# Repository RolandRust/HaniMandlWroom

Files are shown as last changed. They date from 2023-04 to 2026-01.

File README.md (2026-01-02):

# HaniMandlWroom
HaniMandel für das Node MCU ESP32 38Pin Evaluation Board<br>

## Kompiliert nur mit Visual Studio Code. Mit der Arduino IDE gibts Probleme!

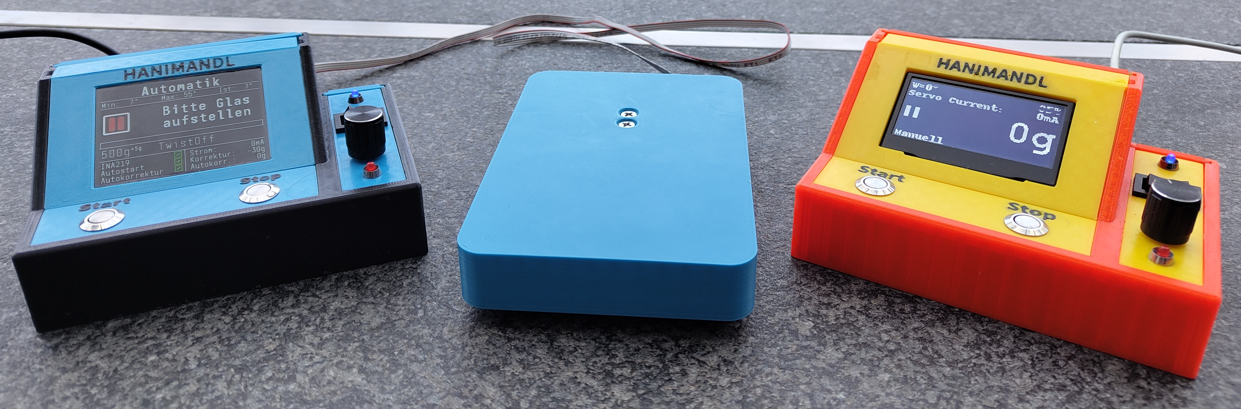
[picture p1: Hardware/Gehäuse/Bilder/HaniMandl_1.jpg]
HaniMandl_1


Dies ist eine abgeänderte Version von dem Orginal HaniMandl Projekt. Die Idee und Veröffentlichung wurde auf der Facebook-Gruppe ["Imkerei und Technik. Eigenbau"](https://www.facebook.com/groups/139671009967454) veröffentlicht.
Als Grundlage für dieses Projekt bediente ich mich am [develop Branch (V0.2.13)](https://github.com/ClemensGruber/hani-mandl/tree/develop) von Clemens Gruber.

## Projekt ligt momentan auf dem Eis

Open Source ist echt genial. Sich damit zu bereichern, ohne auch nur eine Änderung beizutragen, oder einfach nur die eigenen Daten für das Gehäuse zu veröffentlichen, ist einfach doof. Deshalb habe ich das Projekt erstmal auf Eis gelegt. Auch der Dev-Branch wird nicht mehr mit den neuesten Aktualisierungen versorgt. Ich gehe nun einen anderen Weg.

Aus dem kleinen wird der große – aber das wird weniger. Der Dreifach-Switch sowie Start- und Stop-Taster verschwinden. Übrig bleiben nur noch der Rotary-Encoder und ein 4-Zoll-TFT (und sollte ich mich irgendwo geirrt haben, hätte ich noch den Touch als Backup).

Wird es wieder Open Source? Wahrscheinlich nicht – wegen solchen doofen Vögel.

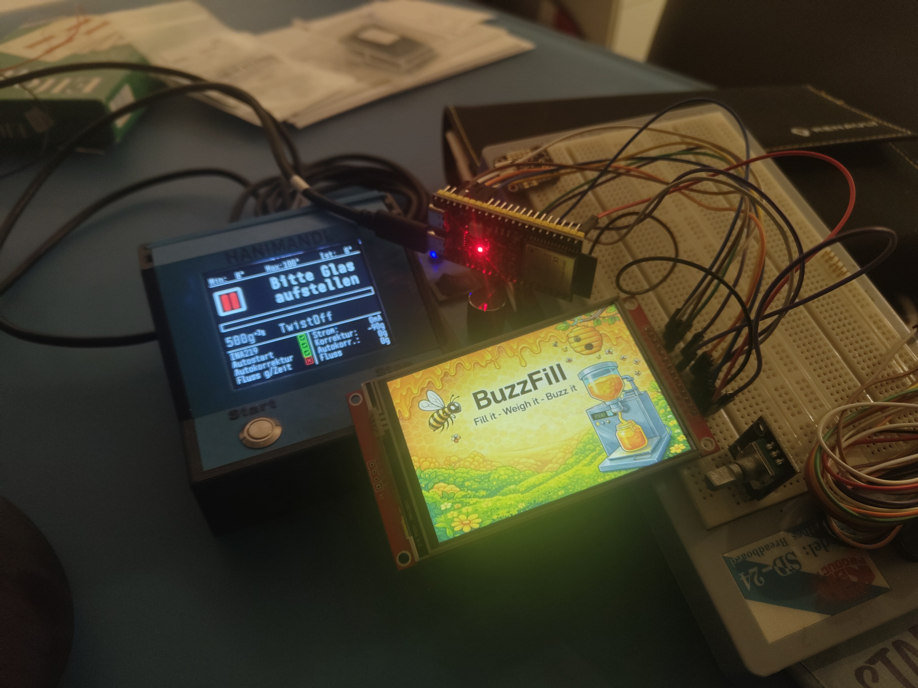
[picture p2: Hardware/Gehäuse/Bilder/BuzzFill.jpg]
BuzzFill


## Einstellungen
```
//
// Usereinstellung
//
// Könnt ihr auf eins lassen. User 2 und User 3 haben andere Glaseinstellungen
//
#define USER 1                    // 1 = Hanimandl Standart (ist die Default Einstellung so wie Ihr es gewohnt seit)
                                  // 2 = Gerold (Wird bei euch nicht funktionieren, da die Logos fehlen im ResPos)
                                  // 3 = Roli

//
// Hier den Code auf die verwendete Hardware einstellen
//
#define HARDWARE_LEVEL 1          // 1 = ESP32-WROOM 38Pin Connector
                                  // 2 = Heltec WiFi Kit V3 use on board display (nur in Verbindung mit DISPLAY_TYP 1)
                                  // 3 = Heltec WiFi Kit V3 use extern display   (nur in Verbindung mit DISPLAY_TYP 1)
#define SCALE_TYP 2               // 1 = 2kg Wägezelle
                                  // 2 = 5kg Wägezelle
#define SERVO_ERWEITERT           // definieren, falls die Hardware mit dem alten Programmcode mit Poti aufgebaut wurde oder der Servo zu wenig fährt
                                  // Sonst bleibt der Servo in Stop-Position einige Grad offen! Nach dem Update erst prüfen!
#define ROTARY_SCALE 1            // in welchen Schritten springt unser Rotary Encoder. 
                                  // Beispiele: KY-040 = 2, HW-040 = 1, für Poti-Betrieb auf 1 setzen
#define DISPLAY_TYPE 3            // 1 = 128x64 pixel OLED Display angeschlossen über I2C
                                  // 2 = 128x64 pixel OLED Display angeschlossen über SPI (nicht für das Heltec Module)
                                  // 3 = 320x240 pixel TFT Display ST7789 angeschlossen über SPI (nicht für das Heltec Module)
                                  // 99 = Oled über I2C und TFT über SPI für development
#define OTA 1                     // 0 = OTA Uptade ausgeschalten
                                  // 1 = OTA Update eingeschalten
#define DREHTELLER 0              // 0 = kein Drehteller
                                  // 1 = Drehteller vorhanden
#define CHANGE_MAC_ADDRESS_HM 1   // 0 = behalte die Orginale Mac Adresse
                                  // 1 = Wechsle die Mac Adresse auf {0x74, 0x00, 0x00, 0x00, 0x00, 0x01}
#define CHANGE_MAC_ADDRESS_TT 1   // 0 = Mac Adresse vom Drehteller ist die orginale
                                  // 1 = Mac Adresse vom Drehteller wurde gewechselt auf {0x74, 0x00, 0x00, 0x00, 0x00, 0x02}
//#define FEHLERKORREKTUR_WAAGE   // falls Gewichtssprünge auftreten, können diese hier abgefangen werden
                                  // Achtung, kann den Wägeprozess verlangsamen. Vorher Hardware prüfen.
//#define QUETSCHHAHN_LINKS       // Servo invertieren, falls der Quetschhahn von links geöffnet wird. Mindestens ein Exemplar bekannt

//
// Ende Benutzereinstellungen!
// 
```

## OTA Update
Neu kann man auch über WLAN eine neue Firmware aufspielen.
Diese Funktion wurde mit Hilfe von ElegantOTA implementiert: https://github.com/ayushsharma82/ElegantOTA
```
#define OTA 1                     // 0 = OTA Uptade ausgeschalten
                                  // 1 = OTA Update eingeschalten
```
Die SSID und das Passwort wird in dem File ./src/Resources/wifi.h eingetragen.
Um das OTA zu aktivieren betätigt die Start Taste wärend Ihr im Setupmenü Hauptbildschirm seid. Danach verbindet sich der HM mit dem WLAN und wenn es klappt wird die IP-Adresse angeteigt.
Diese könnt Ihr nun an eurem Computer eingeben (z.B. http://192.168.76.232/update) und danach ein Beliebiges Binary File über den Browser flaschen.  

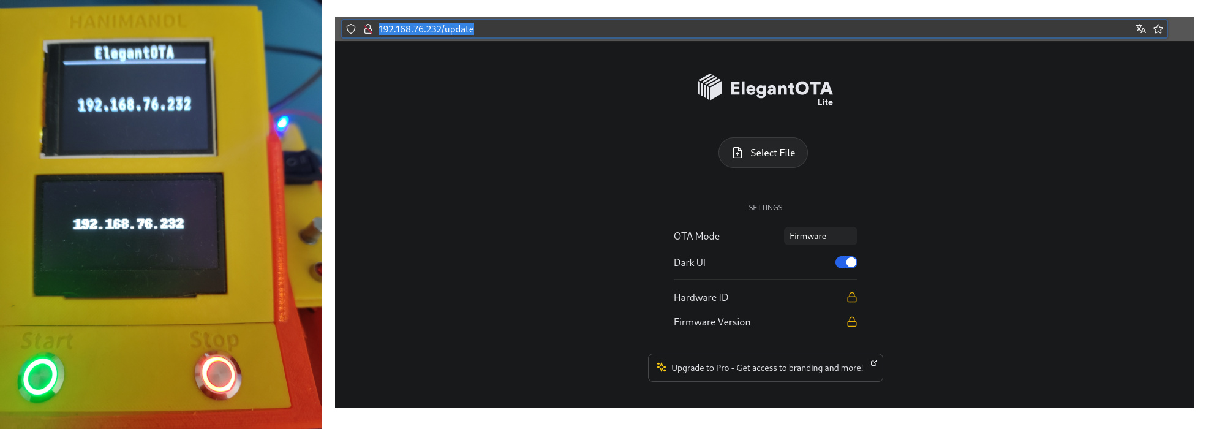
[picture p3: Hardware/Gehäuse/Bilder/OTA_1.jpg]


## Automatischer Volumenstrom beim Abfüllen
Unter Setup - Automatik kann neu ein Automatisch geregelter Volumenstrom eingestellt werden. Dies kan Hilfreich sein, wenn sehr flüssiger Honig abgefüllt wird.

## Bekannte Käferlein
Beim ersten Start ist der maximale Öffnungswinkel im Manuel und Automatik Betrieb auf 0. Dieser muss dann mit der Rotary eingestellt werden. Danach wird der Wert gespeichert. Ob das in der Alten Version auch schon so war, kann ich aus dem Kopf nicht sagen :-)

## Changelog
W.0.2
- OTA update implementiert
- Automatischer Volumenstrom beim Abfüllen implementiert (Nicht von mir getestet)
- Der HM kann nun auch über eine Sprachdatei die Menüsprache ändern (implementiert wurde bis jetzt Deutsch und Englisch)

W.0.3
- Die Sprache kann nun im Setup Menü ausgewählt werden (momentan Deutsch und Englisch. Ihr dürft gerne neue Sprachdateien machen und mir zukommen lassen)
- Funktion implementiert bei welcher man nach dem Tara das Glas wegnehmen kann und wider draufstellen mit eider Honigwabe oder sonstigem drin. (kann im Automatik Menü eingestellt werden)
- Hardware Level 2 und 3 hinzugefügt. Heltec Wifi Kit V3 (geht nur mit OLED Display)
- Drehteller Integriert

## Copyright

Die Software unterliegt dem gleichen Coryright und Anforderungen wie das Hauptprojekt.
Die Hardware (Gehäuse und PCB) sind von mir gemacht worden. Ich verzichte auf ein Copyriht für den Eigengebrauch. Auch wenn ich den Hanimandel nicht kommerziell vertreibe, gehören mir die Daten vom Gehäuse und PCB und diese dürfen nicht ohne meine Zustimmung kommerziell benützt werden.

## Benutzte Programme und Lizensen

Gehäuse: Ondsel/FreeCAD (keine Lizenz notwendig)<br>
PCB: DipTrace (kommerzielle Lizenz)

## Drehteller addon für den HaniMandel (HonigSchleppElesl)

zu finden unter: https://github.com/RolandRust/HonigSchleppElesl/

## Appell an dich

Bringt nix :-)

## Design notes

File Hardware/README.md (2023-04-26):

# HaniMandlWroom/Hardware
HaniMandel für das Node MCU ESP32 38Pin Evaluation Board
## Was findet man in diesem Ordner
In diesem Ordner findet man alles was mir der Hardware von HaniMandel zu tun hat

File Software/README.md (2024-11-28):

# HaniMandlWroom/Hardware
HaniMandel für das Node MCU ESP32 38Pin Evaluation Board
## Was findet man in diesem Ordner
In diesem Ordner findet man alles was mir der Software vom HaniMandel zu tun hat
## Einstellungen
```
//
// Usereinstellung
//
// Könnt ihr auf eins lassen. User 2 und User 3 haben andere Glaseinstellungen
//
#define USER 3                    // 1 = Hanimandl Standart (ist die default einstellung so wie Ihr es gewohnt seit)
                                  // 2 = Gerold (Wird bei euch nicht funktionieren, da die Logos fehlen im ResPos)
                                  // 3 = Roli

//
// Hier den Code auf die verwendete Hardware einstellen
//
#define HARDWARE_LEVEL 1          // 1 = ESP32-WROOM 38Pin Connector
#define SCALE_TYP 2               // 1 = 2kg Wägezelle
                                  // 2 = 5kg Wägezelle
#define SERVO_ERWEITERT           // definieren, falls die Hardware mit dem alten Programmcode mit Poti aufgebaut wurde oder der Servo zu wenig fährt
                                  // Sonst bleibt der Servo in Stop-Position einige Grad offen! Nach dem Update erst prüfen!
#define ROTARY_SCALE 1            // in welchen Schritten springt unser Rotary Encoder. 
                                  // Beispiele: KY-040 = 2, HW-040 = 1, für Poti-Betrieb auf 1 setzen
#define DISPLAY_TYPE 2            // 1 = 128x64 pixel OLED Display angeschlossen über I2C
                                  // 2 = 128x64 pixel OLED Display angeschlossen über SPI
                                  // 3 = 320x240 pixel TFT Display ST7789 angeschlossen über SPI
                                  // 99 = Oled über I2C und TFT über SPI für development
#define OTA 1                     // 0 = OTA Uptade ausgeschalten
                                  // 1 = OTA Update eingeschalten
#define DREHTELLER 1              // 0 = kein Drehteller
                                  // 1 = Drehteller vorhanden
#define CHANGE_MAC_ADDRESS_HM 1   // 0 = behalte die Orginale Mac Adresse
                                  // 1 = Wechsle die Mac Adresse auf {0x74, 0x00, 0x00, 0x00, 0x00, 0x01}
#define CHANGE_MAC_ADDRESS_TT 1   // 0 = Mac Adresse vom Drehteller ist die orginale
                                  // 1 = Mac Adresse vom Drehteller wurde gewechselt auf {0x74, 0x00, 0x00, 0x00, 0x00, 0x02}
//#define FEHLERKORREKTUR_WAAGE   // falls Gewichtssprünge auftreten, können diese hier abgefangen werden
                                  // Achtung, kann den Wägeprozess verlangsamen. Vorher Hardware prüfen.
//#define QUETSCHHAHN_LINKS       // Servo invertieren, falls der Quetschhahn von links geöffnet wird. Mindestens ein Exemplar bekannt

//
// Ende Benutzereinstellungen!
// 
```

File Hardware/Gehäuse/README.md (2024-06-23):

# HaniMandlWroom/Hardware/Gehäuse
HaniMandel für das Node MCU ESP32 38Pin Evaluation Board
## Was findet man in diesem Ordner
In diesem Ordner findet man alles was man braucht, um das Gehäuse und die Waage mir einem 3D-Drucker zu erstellen.

# 3D Bilder
## Gehäuse HaniMandl
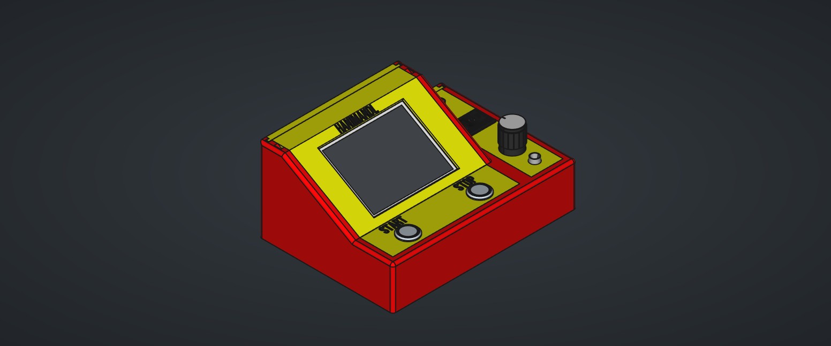
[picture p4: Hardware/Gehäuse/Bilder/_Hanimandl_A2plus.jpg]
Gehäuse HaniMandl

## Gehäuse Waage
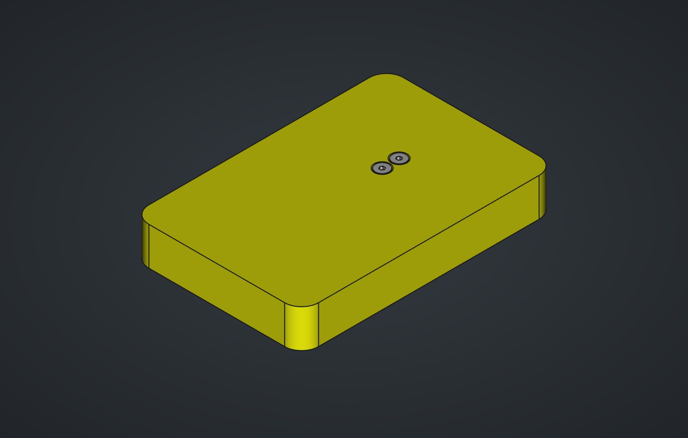
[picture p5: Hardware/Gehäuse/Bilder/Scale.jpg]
Gehäuse Waage


# Einzelteile Gehäuse Hanimandl
## Body (Filename: Bottom)
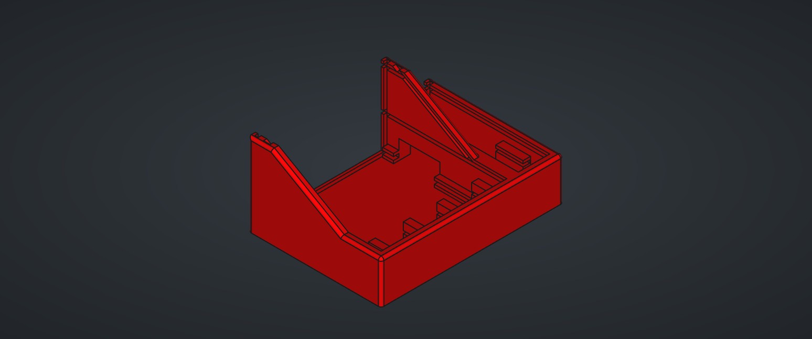
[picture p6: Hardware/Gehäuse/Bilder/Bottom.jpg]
Body

## Start/Stop Taster (Filename: Button)
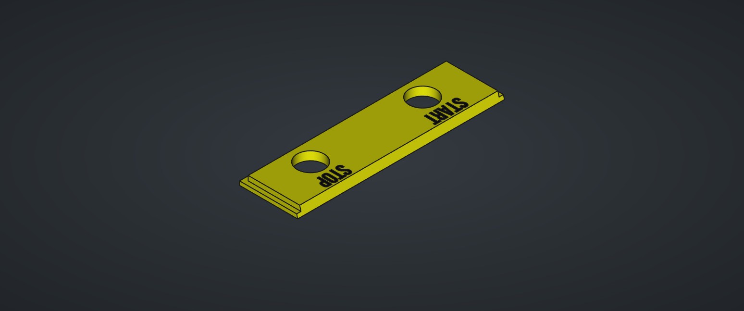
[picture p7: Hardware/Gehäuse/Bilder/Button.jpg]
Start/Stop Taster

## Display (Filename: Display_OLED)
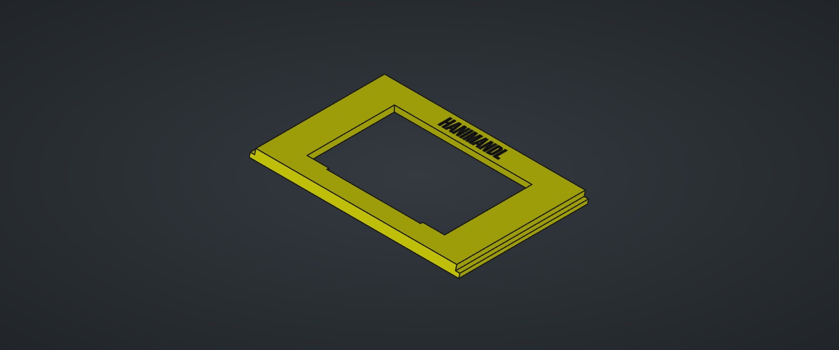
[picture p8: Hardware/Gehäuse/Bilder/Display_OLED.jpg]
Display

## Display 2.8TFT (Filename: Display_TFT)
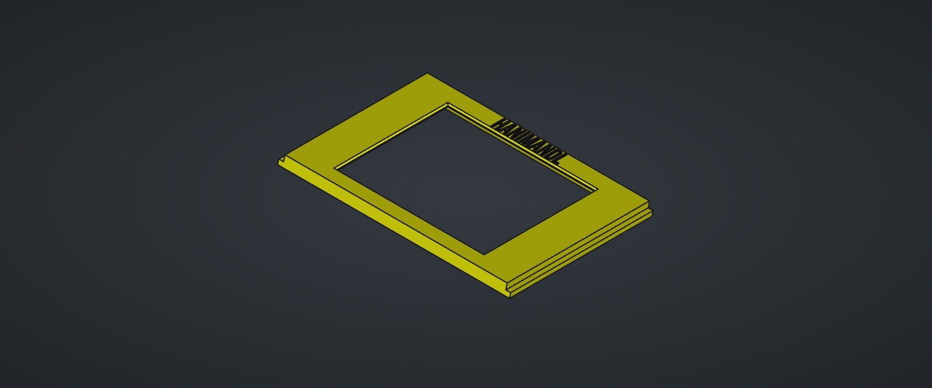
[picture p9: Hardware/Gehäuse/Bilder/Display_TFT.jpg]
Display

## Deckel top klein (Filename: Top)
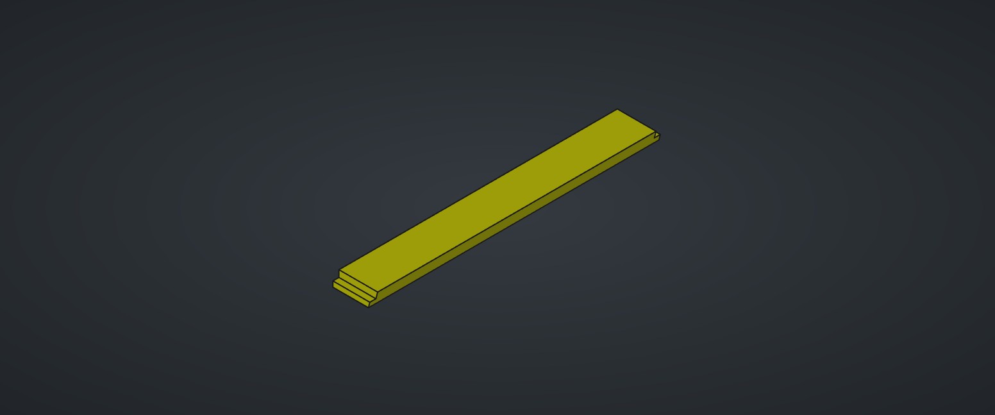
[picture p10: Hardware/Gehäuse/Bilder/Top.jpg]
Deckel top klein

## Deckel Bedienelemente (Filename: Rotary)
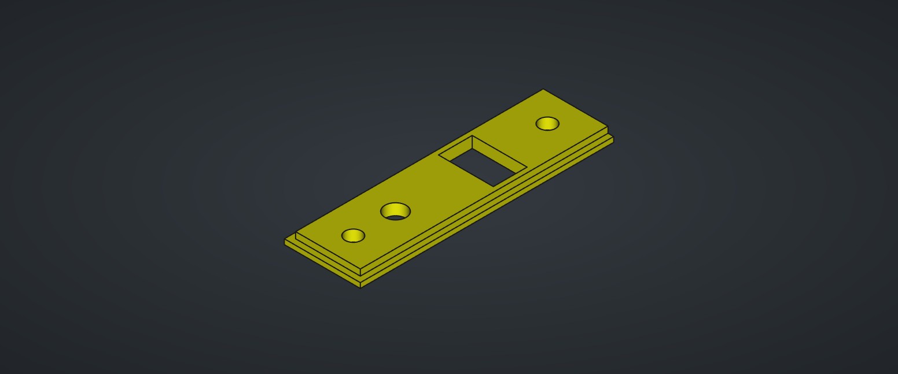
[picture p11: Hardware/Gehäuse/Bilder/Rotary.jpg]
eckel Bedienelemente

## Deckel Rückseite Bedienelemente (Filename: Back_Small)
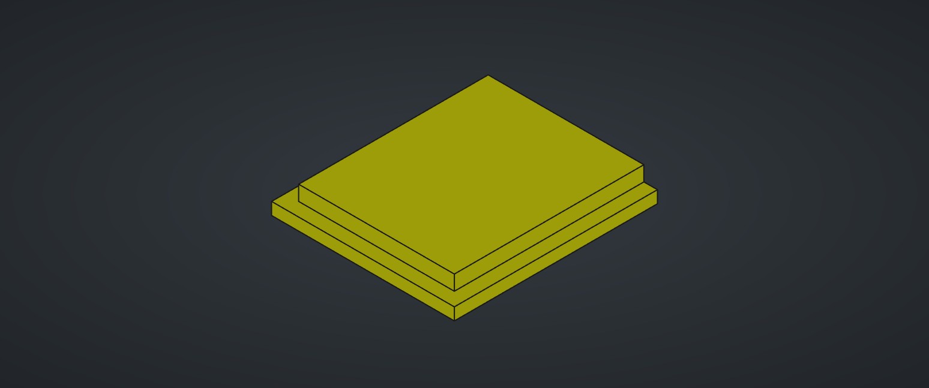
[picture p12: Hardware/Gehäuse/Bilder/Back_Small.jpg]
Deckel Rückseite Bedienelemente

## Deckel Rückseite Display oben (Filename: Back_Big_2)
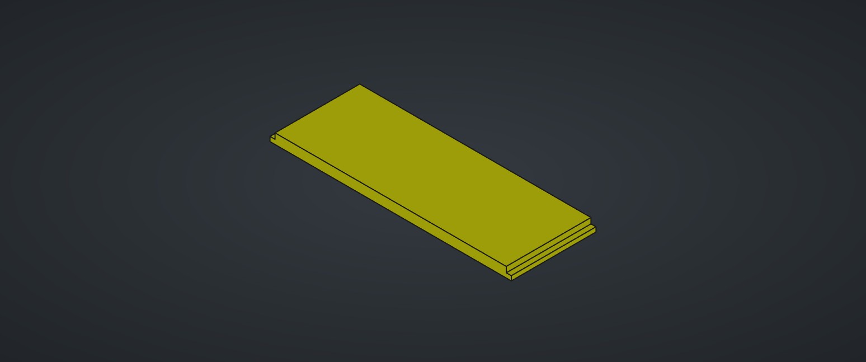
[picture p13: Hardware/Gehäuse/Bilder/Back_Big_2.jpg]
Deckel Rückseite Display oben

## Deckel Rückseite Display unten ohne USB (Filename: Back_Big_1)
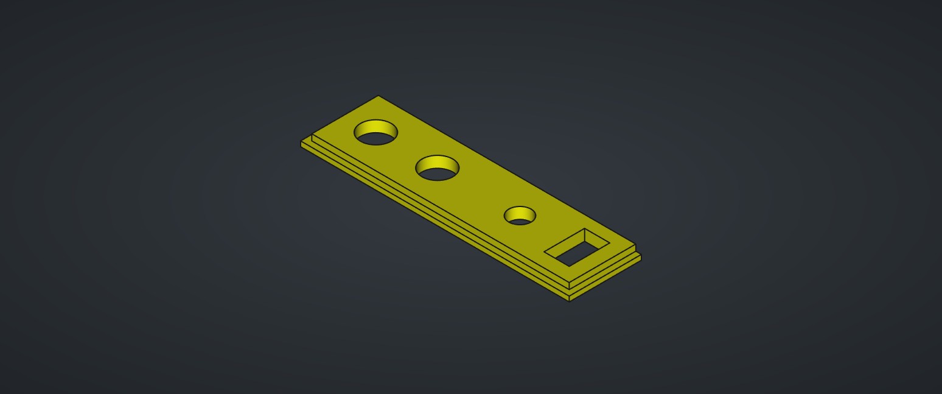
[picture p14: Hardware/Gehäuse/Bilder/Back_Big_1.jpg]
Deckel Rückseite Display unten ohne US

## Deckel Rückseite Display unten mit USB (Filename: Back_Big_1_USB)
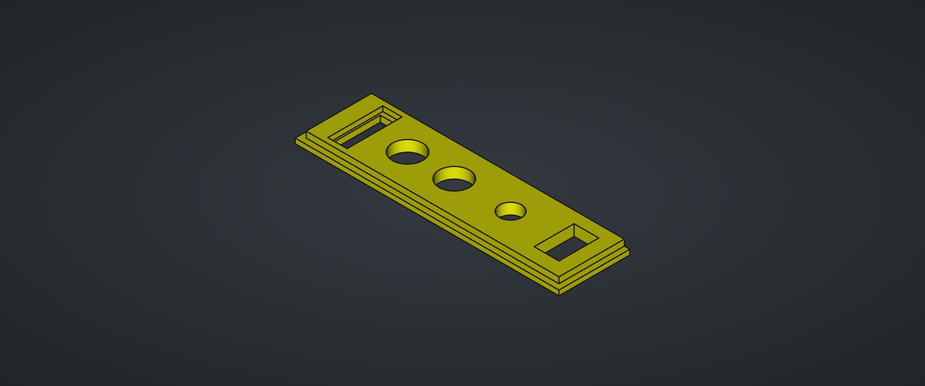
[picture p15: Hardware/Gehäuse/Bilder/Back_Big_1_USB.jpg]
Deckel Rückseite Display unten mit US


# Einzelteile Gehäuse Waage
## Waage oben (Filename: Scale_Top)
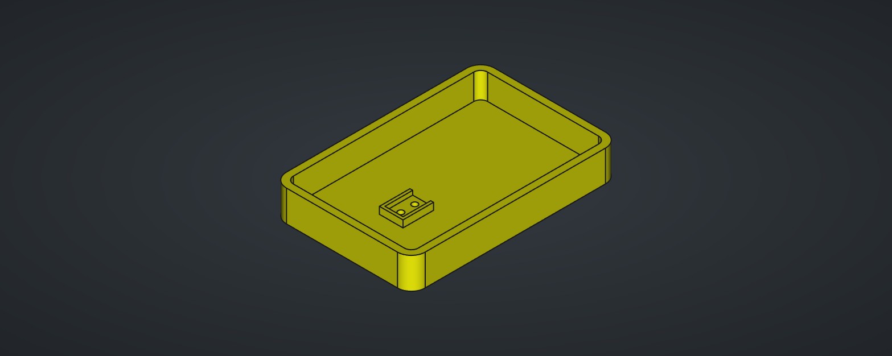
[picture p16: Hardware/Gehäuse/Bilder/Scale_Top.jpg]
Waage oben

## Waage unten (Filename: Scale_Bottom)
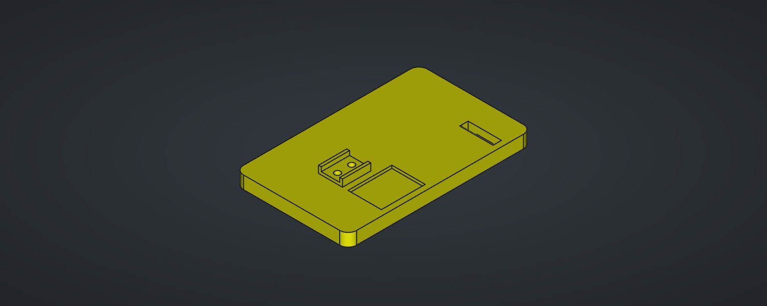
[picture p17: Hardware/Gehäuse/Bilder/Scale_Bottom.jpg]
Waage unten


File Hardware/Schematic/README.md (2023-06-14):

# HaniMandlWroom/Hardware/Schematic
HaniMandel für das Node MCU ESP32 38Pin Evaluation Board
## Was findet man in diesem Ordner
In diesem Ordner findet man alle Schaltpläne für den Hanimandl
## Schematic_Alle_Optionen.pdf
Vollbestückung mit allen Bestückungsoptionen
## Schematic_I2C-Display_No-INA219
Bestückungsoption mit einem I2C OLED 128x64 Pixel (SSD1306/SSD1309) und ohne INA219
## Schematic_I2C-Display_With-INA219
Bestückungsoption mit einem I2C OLED 128x64 (SSD1306/SSD1309) Pixel und mit INA219
## Schematic_SPI-Display_No-INA219
Bestückungsoption mit einem SPI OLED 128x64 Pixel (SSD1306/SSD1309) und ohne INA219<br>
TFT Display angesteuert über SPI mir 320x240 Pixel und dem ST7735 Displaytreiber und ohne INA219
## Schematic_SPI-Display_With-INA219
Bestückungsoption mit einem SPI OLED 128x64 (SSD1306/SSD1309) Pixel und mit INA219<br>
TFT Display angesteuert über SPI mir 320x240 Pixel und dem ST7735 Displaytreiber und mit INA219

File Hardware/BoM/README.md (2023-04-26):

# HaniMandlWroom/Hardware/BoM
HaniMandel für das Node MCU ESP32 38Pin Evaluation Board
## Was findet man in diesem Ordner
In diesem Ordner findet man die BoM für alle Bestückungswarianten von dem HaniMandl.

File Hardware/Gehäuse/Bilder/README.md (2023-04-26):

# HaniMandlWroom/Hardware/Gehäuse/Bilder
HaniMandel für das Node MCU ESP32 38Pin Evaluation Board
## Was findet man in diesem Ordner
In diesem Ordner findet man nur Bilder von dem Gehäuse des HaniMandels und der Waage

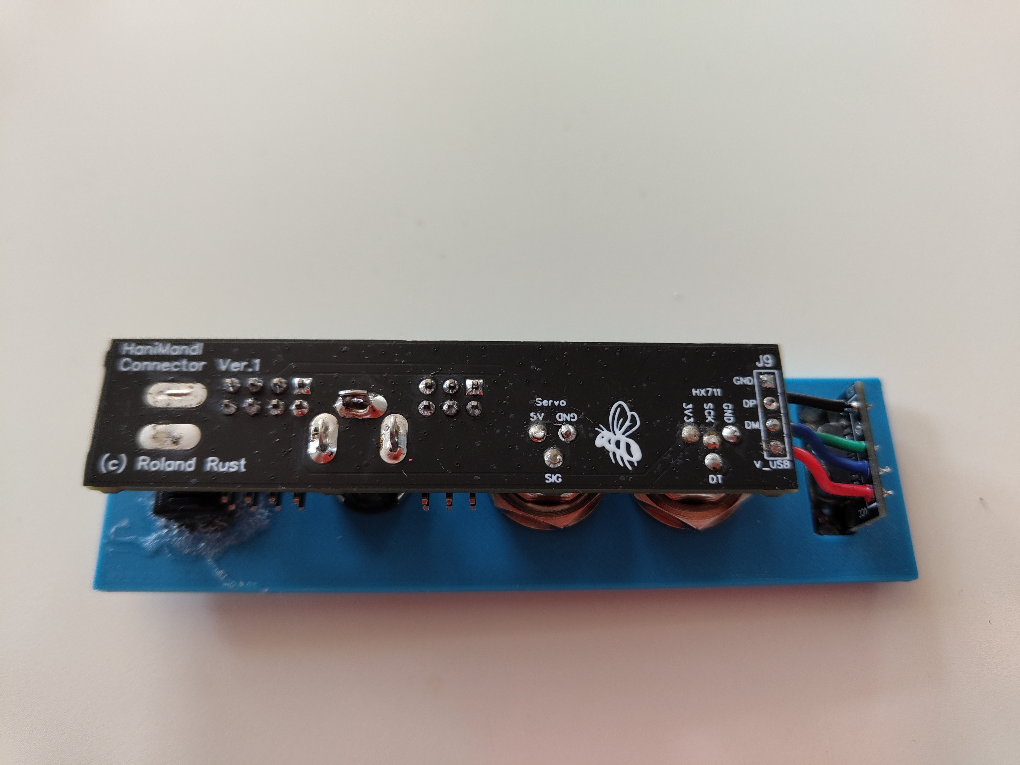
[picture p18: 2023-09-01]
Hardware/PCB/Pictures/363501928_1014343573054529_2882119520657273659_n.jpg

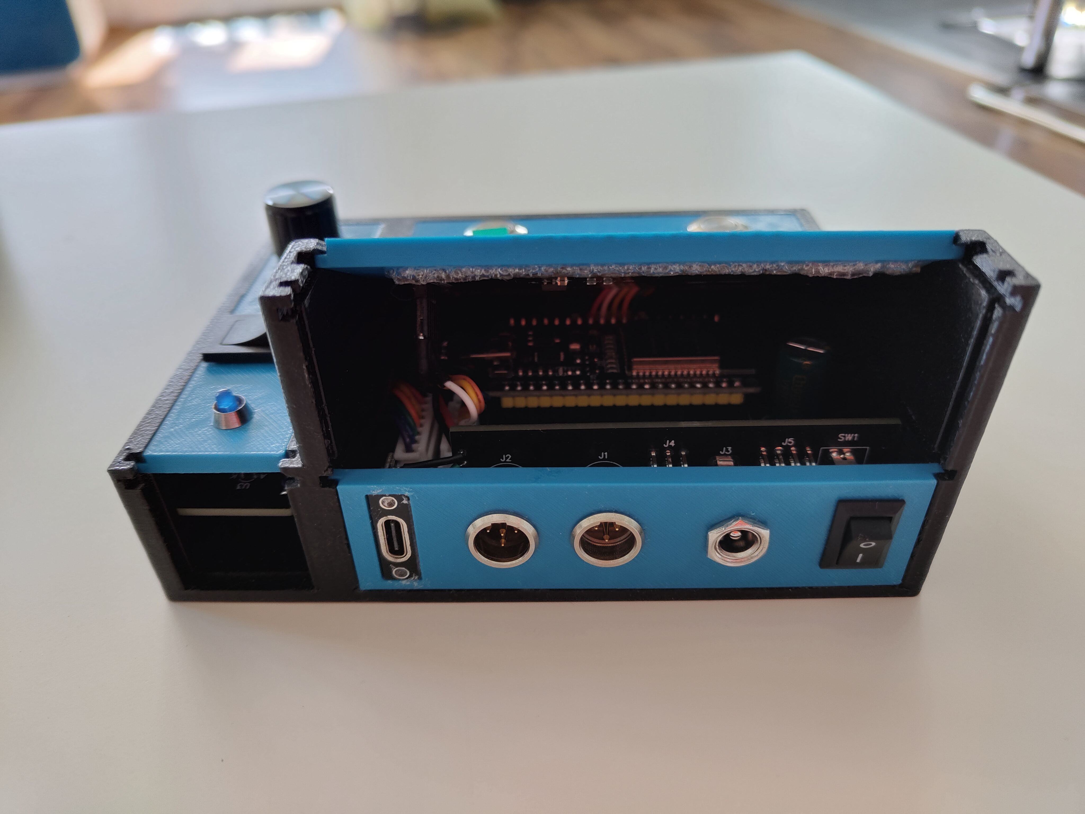
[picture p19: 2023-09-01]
Hardware/PCB/Pictures/363467502_966205168005585_3297736577394320761_n.jpg

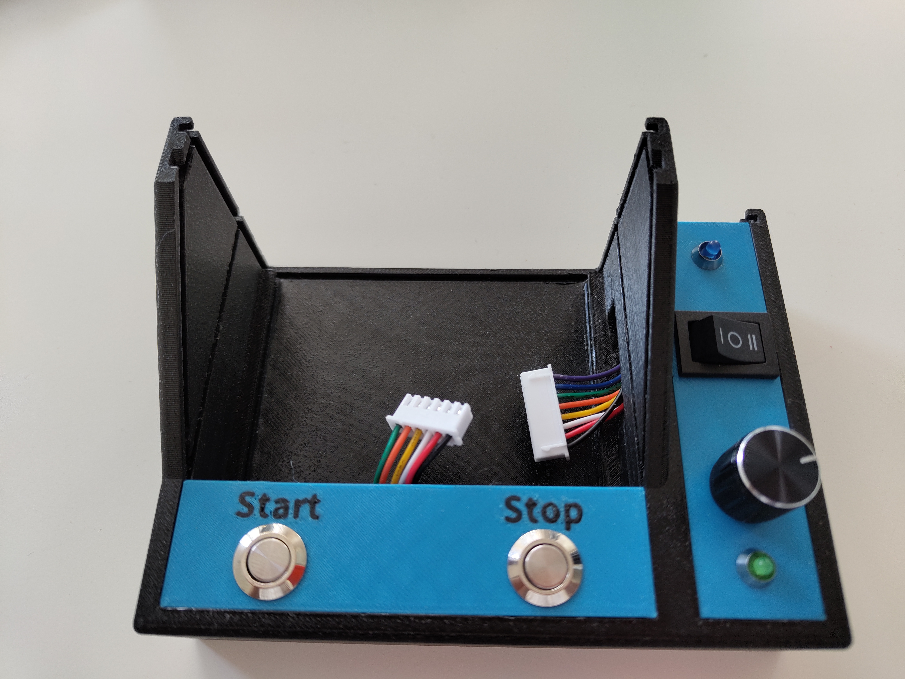
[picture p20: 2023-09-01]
Hardware/PCB/Pictures/363482455_1355187868746263_7550727053654712508_n.jpg

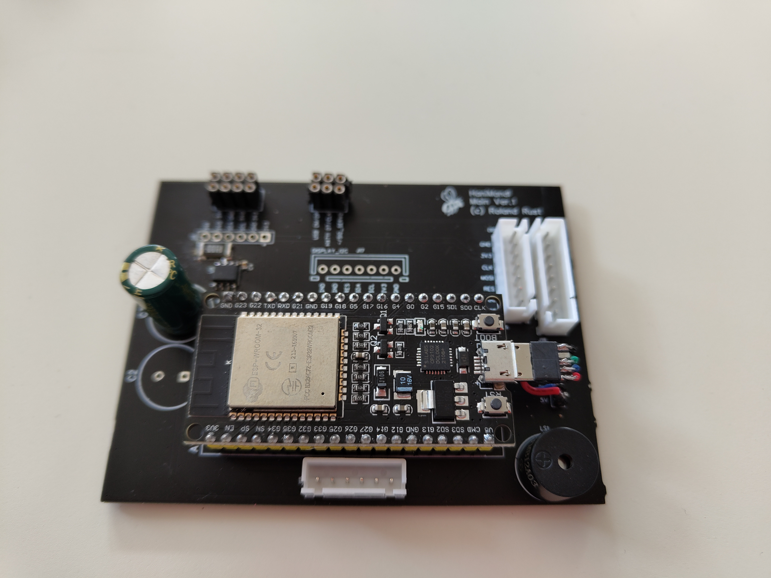
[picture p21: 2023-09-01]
Hardware/PCB/Pictures/363498172_692735799364409_5890090656269243421_n.jpg

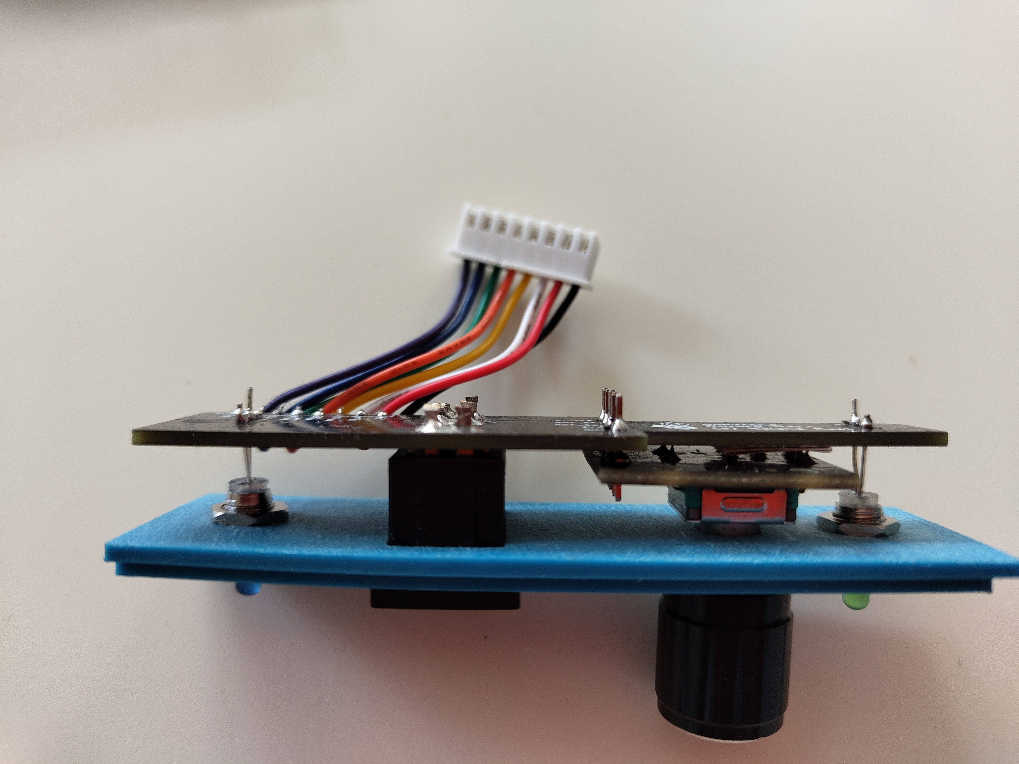
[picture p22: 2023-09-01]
Hardware/PCB/Pictures/363483665_819673566153577_7103739130340940338_n.jpg

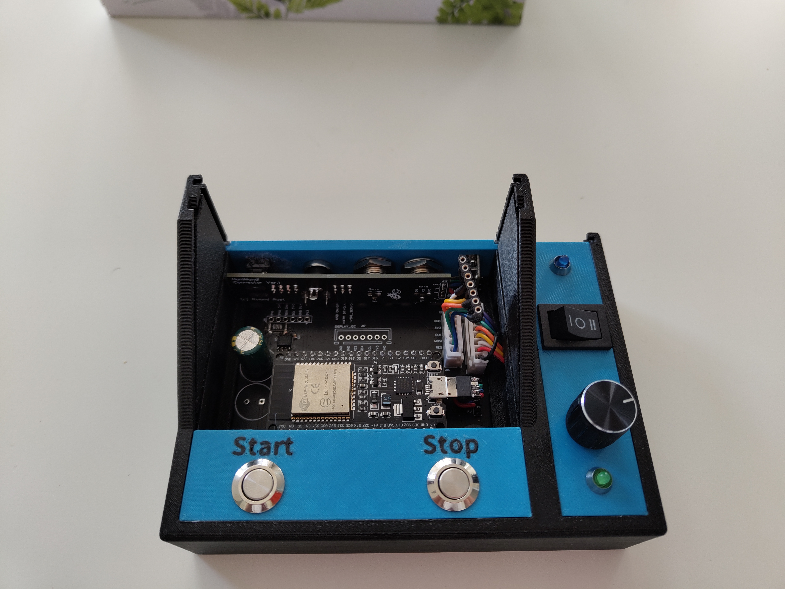
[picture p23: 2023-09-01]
Hardware/PCB/Pictures/363481905_1242739086406891_790757974748476911_n.jpg

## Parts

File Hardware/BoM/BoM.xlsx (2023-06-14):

 | Var1 | I2C OLED Display ohne INA219
 | Var2 | I2C OLED Display mit INA219
 | Var3 | SPI OLED Display ohne INA219
 | Var4 | SPI OLED Display mit INA219
 | Var5 | SPI TFT Display ohne INA219
 | Var6 | SPI TFT Display mit INA219
 | Hauptgehäuse
# | RefDes | Name | Quantity | Var1 | Var2 | Var3 | Var4 | Var5 | Var6 | Aliexpress Link (kann sein das er auf einmal nicht mehr funktioniert)
1 | - | Lochplatine 70x90mm | 1 | x | x | x | x | x | x | https://de.aliexpress.com/item/4000826804819.html
2 | A1 | Node MCU ESP32 38Pin Entwicklungsboard mit Wroom Modul | 1 | x | x | x | x | x | x | https://de.aliexpress.com/item/1005001636295529.html
3 | C1 | Elektrolyth Kondensator 2u2 | 1 | x | x | x | x | x | x
4 | LS1 | Buzzer (Tröte) | 1 | x | x | x | x | x | x | https://de.aliexpress.com/item/32885950305.html
5 | U1, U2 | Taster 2pol 12mm | 2 | x | x | x | x | x | x | https://de.aliexpress.com/item/4000310874353.html
6 | - | Leuchtdioden Halterung 3mm Metal | 2 | x | x | x | x | x | x | https://de.aliexpress.com/item/1005003385738351.html
7 | D1, D2 | Leuchtdioden 3mm | 2 | x | x | x | x | x | x | https://de.aliexpress.com/item/1005003432647675.html
8 | R1 | Widerstand 30K | 1 | x | x | x | x | x | x
9 | R2 | Widerstand 10K | 1 | x | x | x | x | x | x
10 | SW1 | Rotray Encoder mit Drehknopf (KY-040 oder HW-040) | 1 | x | x | x | x | x | x | https://de.aliexpress.com/item/1005001506432012.html
11 | U6 | SPDT On/Off/On Schalter 21x15mm | 1 | x | x | x | x | x | x | https://de.aliexpress.com/item/32986572167.html
12 | U3 | SPST Schalter 15x10mm | 1 | x | x | x | x | x | x | https://de.aliexpress.com/item/32987717201.html
13 | J1 | Power Buchse 2.1x5.5mm | 1 | x | x | x | x | x | x | https://de.aliexpress.com/item/32790883652.html
14 | U5 | Mini XLR Buchse 3Pin | 1 | x |  | x |  | x |  | https://de.aliexpress.com/item/1005004521851490.html?curPageLogUid=nE3oQnMNPnsI
15 | U7 | Mini XLR Buchse 3Pin | 1 |  | x |  | x |  | x
16 | U4 | Mini XLR Buchse 4Pin | 1 | x | x | x | x | x | x
17 | IC3 | INA219 Modul | 1 |  | x |  | x |  | x | https://de.aliexpress.com/item/1005004840860104.html
18 | IC1 | OLED Display 2.42 Zoll 126x64 | 1 | x | x |  |  |  |  | https://de.aliexpress.com/item/1005002766729064.html
19 | IC2 | OLED Display 2.42 Zoll 126x64 | 1 |  |  | x | x
20 | IC? | TFT Display 2.8 Zoll 320x240 | 1 |  |  |  |  | x | x | https://de.aliexpress.com/item/4000832671813.html
21 | - | Kabel mit Stecker um die Komponenten auf die Platine zu bringen |  | x | x | x | x | x | x | https://de.aliexpress.com/item/33011451583.html
 |  | Oprional wenn der USB Anschluss von dem Module nach ausen geführt wird
22 | - | USB C Buchse | 1 | x | x | x | x | x | x | https://de.aliexpress.com/item/1005003446036071.html
23 | - | Micro USB Stecker | 1 | x | x | x | x | x | x | https://de.aliexpress.com/item/32646590601.html
 | Waage
24 | - | Wäägezelle 5Kg | 1 | x | x | x | x | x | x | https://de.aliexpress.com/item/1005002483530537.html
25 | - | HX711 Module | 1 | x | x | x | x | x | x | https://de.aliexpress.com/item/33041823995.html?curPageLogUid=XPLqdXU4JuIP
 | Abfülleimer
26 |  | Servo 20Kg | 1 | x | x | x | x | x | x | https://de.aliexpress.com/item/32880295279.html
 | Abfülleimer
27 | - | Ein gutes 5V Netzteil | 1 | x | x | x | x | x | x

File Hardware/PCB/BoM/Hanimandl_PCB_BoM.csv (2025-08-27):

# | Quantity | RefDes | Manufacturer | Order Number | Description
1 | 1 | A1 | Diverse | - | ESP32 NodeMCU Module WLAN WiFi Development Board (use PinHeader to connect the Module))
2 | 2 | C1, C5 | Murata | GRM188R71E104K | Chip Monolithic Ceramic Capacitor X7R
3 | 2 | C2, C3 | Chemi-Con | EKMQ160ETD222MJ20S | Miniature Aluminium Electrolytic Capacitor 2200uF 16V ±20% 10x20mm
4 | 1 | D1 | Nexperia | NSR0130P2T5G | 30V Schottky Barrier Diode, 30V / 100mA, 2-Pin SOD-923
5 | 1 | J1 | Spectra | 7102-M3M | Mini XLR Connector 3pol. male
6 | 1 | J2 | Spectra | 7102-M4M | Mini XLR Connector 4pol. male
7 | 1 | J3 | Lumberg | 1614 19 | 2.1mm Power Plug
8 | 1 | J4 | Harwin | M20-9740346 | Pin Header 100min 2x3 right angle
9 | 1 | J5 | Harwin | M20-9740446 | Pin Header 100min 2x4 right angle
10 | 2 | J6, J7 | Bomin Electronic | EJ12-211PM | Ultra Short Metal Button
11 | 3 | J8, J10, J11 | Samtec | TSW-104-07-G-S | 1x4 Pol Connector 100mil
12 | 2 | J9, J19 | Samtec | TSW-104-07-G-S | 1x4 Pol Connector 100mil
13 | 1 | J12 | Samtec | TSW-104-07-G-S | 1x4 Pol Connector 100mil
14 | 1 | J13 | Preci-dip | 803-87-006-65-001101 | Socket 2x3, 2.54mm, height 7mm
15 | 1 | J14 | Preci-dip | 803-87-008-65-001101 | Socket 2x4, 2.54mm, height 7mm
16 | 1 | J15 | Diverse | - | JST XH 6pol Connector 2.54mm (not orginal JST standart)
17 | 2 | J16, J17 | Diverse | - | JST XH 7pol Connector 2.54mm (not orginal JST standart)
18 | 1 | J18 | Diverse | - | JST XH 8pol Connector 2.54mm (not orginal JST standart)
19 | 1 | LS1 | Soberton Inc. | WST-1203UX | AUDIO INDICATOR 82 DB 3 VDC 2300 HZ
20 | 1 | R1 | YAGEO | RC0603JR-0715KL | SMD-Resistor 15kOhm 5 % 100mW 0603
21 | 2 | R2, R7 | YAGEO | PE2512FKE7W0R1L | Resistor 0R1 1% 2W 2512
22 | 4 | R3, R4, R8, R9 | YAGEO | RC0603JR-0710KL | SMD-Resistor 10kOhm 5 % 100mW 0603
23 | 1 | R5 | YAGEO | RC0603JR-071KL | SMD-Resistor 1kOhm 5 % 100mW 0603
24 | 1 | R6 | YAGEO | RC0603JR-0730KL | SMD-Resistor 30kOhm 5 % 100mW 0603
25 | 1 | SW1 | Yueqing Hegxing Electrical | KCD1-11 | 2 pin ON - OFF small rocker switch
26 | 1 | SW2 | IDUINO | SE055 | Rotary Encoder development board, KY-040
27 | 2 | U1, U5 | Texas Instruments | INA219BIDR | INA219 Zero-Drift, Bidirectional Current/Power Monitor with I2C interface
28 | 1 | U2 | Yueqing Hegxing Electrical | KCD1-00-103 | Rocker Switch 6A@250VAC ON-OFF-ON SPST
29 | 1 | U3 | QUADRIOS | 2111O151 | LED blue, 3mm
30 | 1 | U4 | QUADRIOS | 2111O155 | LED red, 3mm

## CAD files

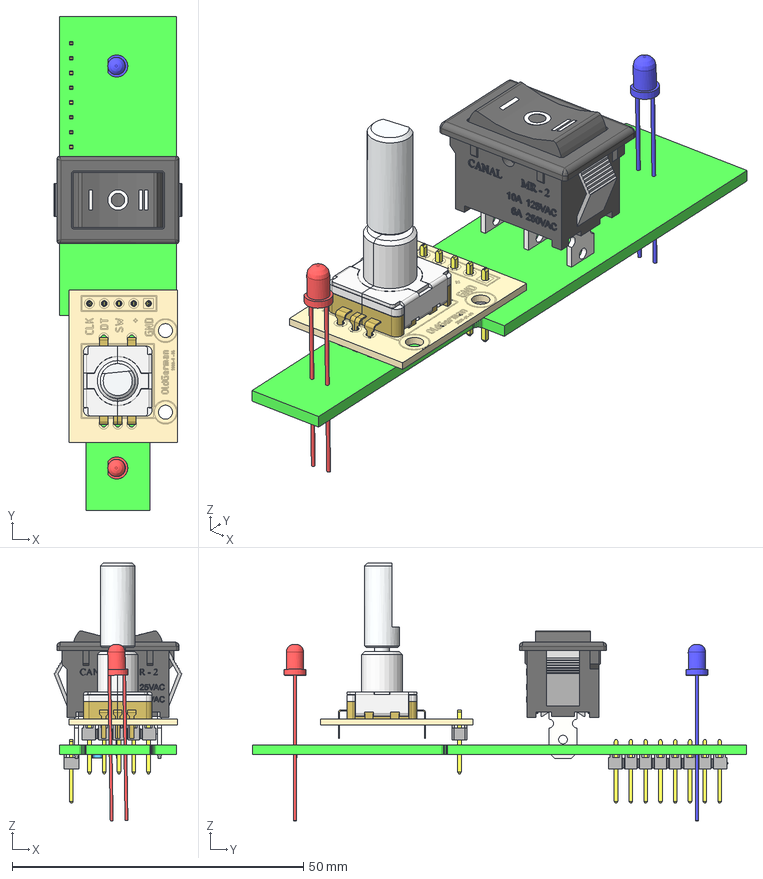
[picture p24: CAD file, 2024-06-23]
Hardware/Gehäuse/Ondsel(FreeCAD)/_STEP_PCB_Rotary.FCStd
21.9 x 84.8 x 44.3 mm
Board__Rotary
TSW-108-07-G-S
TSW-108-07-G-S006
RES_0603
RES_0607
KY-040_Rotary_Encoder_1
KY-040_Rotary_Encoder_019
KY-040_Rotary_Encoder_020
KY-040_Rotary_Encoder_021
KY-040_Rotary_Encoder_022
KY-040_Rotary_Encoder_023
KY-040_Rotary_Encoder_024
KY-040_Rotary_Encoder_025
Rocker_Switch_-_On-Off-On_05
Rocker_Switch_-_On-Off-On_041
Rocker_Switch_-_On-Off-On_042
Rocker_Switch_-_On-Off-On_043
Rocker_Switch_-_On-Off-On_044
Rocker_Switch_-_On-Off-On_045
Rocker_Switch_-_On-Off-On_046
Rocker_Switch_-_On-Off-On_047
Rocker_Switch_-_On-Off-On_048
Rocker_Switch_-_On-Off-On_049
Rocker_Switch_-_On-Off-On_050
Rocker_Switch_-_On-Off-On_051
Rocker_Switch_-_On-Off-On_052
Rocker_Switch_-_On-Off-On_053
Rocker_Switch_-_On-Off-On_054
Rocker_Switch_-_On-Off-On_055
Rocker_Switch_-_On-Off-On_056
LED_3mm_Head_blue
LED_3mm_Head_blue006
LED_3mm_Head_red
LED_3mm_Head_red006

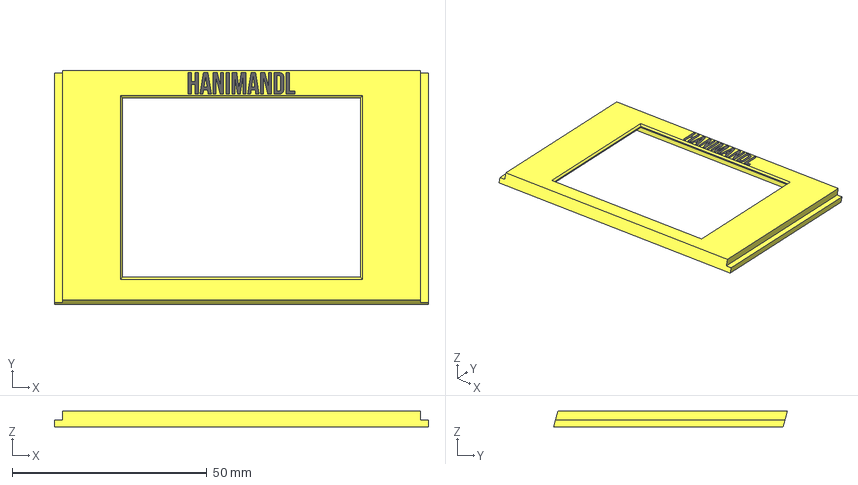
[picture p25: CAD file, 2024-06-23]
Hardware/Gehäuse/STEP/Display_TFT.step
96.0 x 60.0 x 4.00 mm

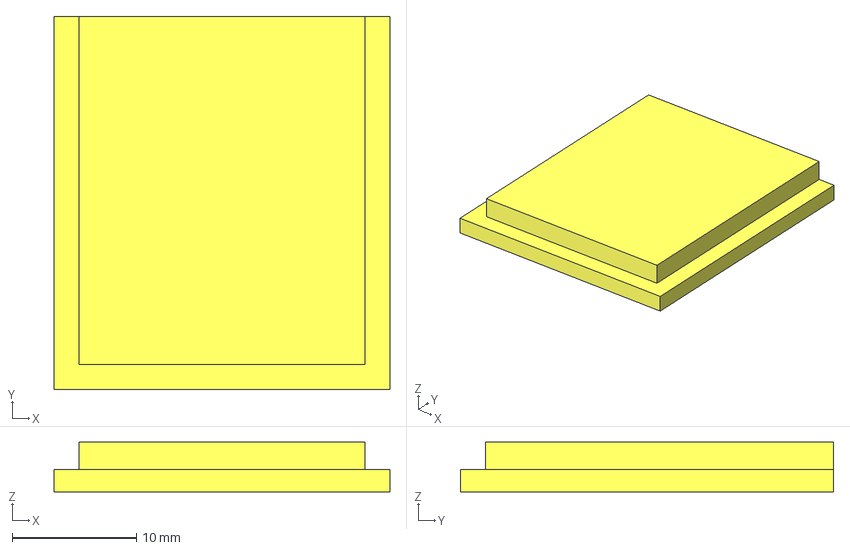
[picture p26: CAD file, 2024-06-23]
Hardware/Gehäuse/Ondsel(FreeCAD)/Back_Small.FCStd
27.0 x 30.0 x 4.00 mm

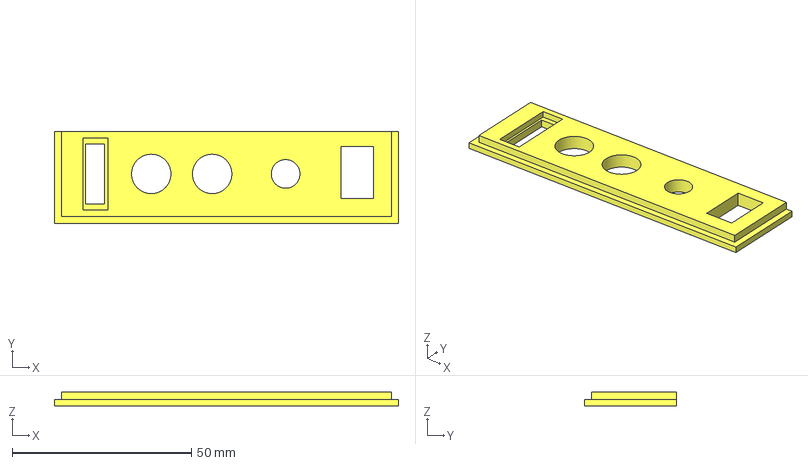
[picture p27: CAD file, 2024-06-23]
Hardware/Gehäuse/Ondsel(FreeCAD)/Back_Big_1_USB.FCStd
96.0 x 25.8 x 4.00 mm

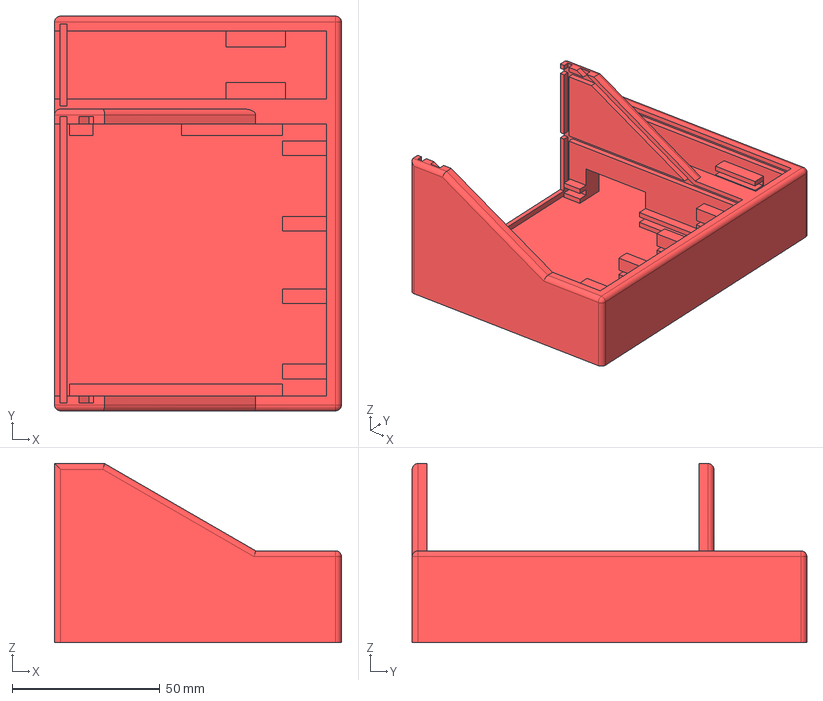
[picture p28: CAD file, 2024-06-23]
Hardware/Gehäuse/STEP/Bottom.step
97.0 x 133.4 x 60.5 mm

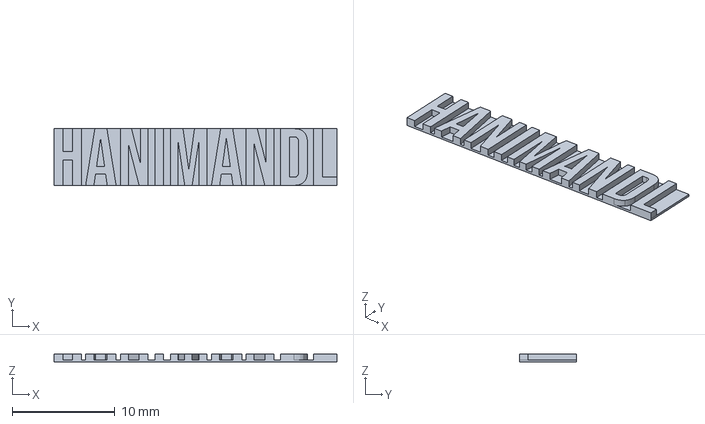
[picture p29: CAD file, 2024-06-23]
Hardware/Gehäuse/Ondsel(FreeCAD)/Hanimandl.FCStd
27.5 x 5.50 x 0.8 mm

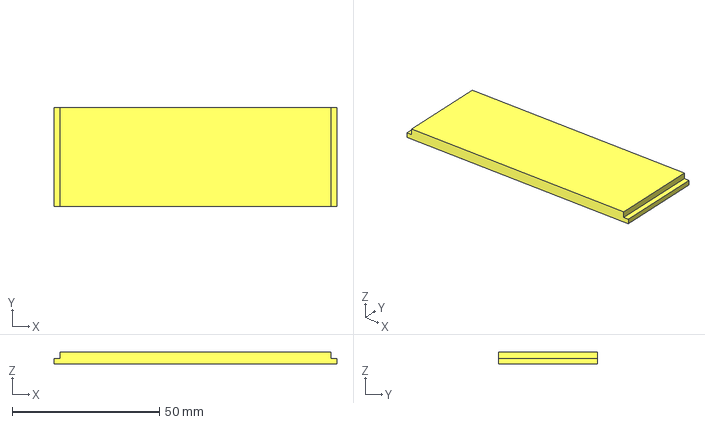
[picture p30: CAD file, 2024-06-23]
Hardware/Gehäuse/STEP/Back_Big_2.step
96.0 x 33.7 x 4.00 mm

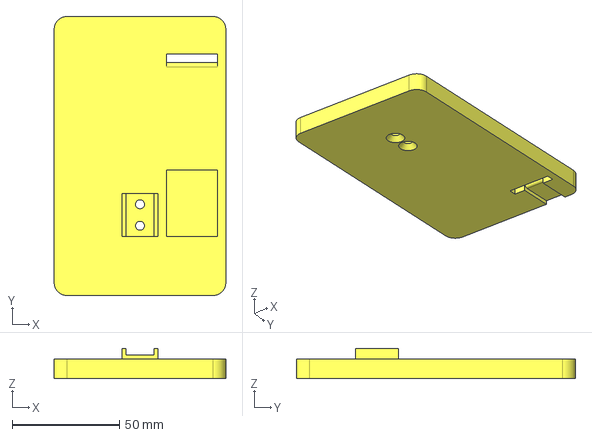
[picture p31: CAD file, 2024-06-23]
Hardware/Gehäuse/Ondsel(FreeCAD)/Scale_Bottom.FCStd
80.0 x 130.0 x 14.0 mm

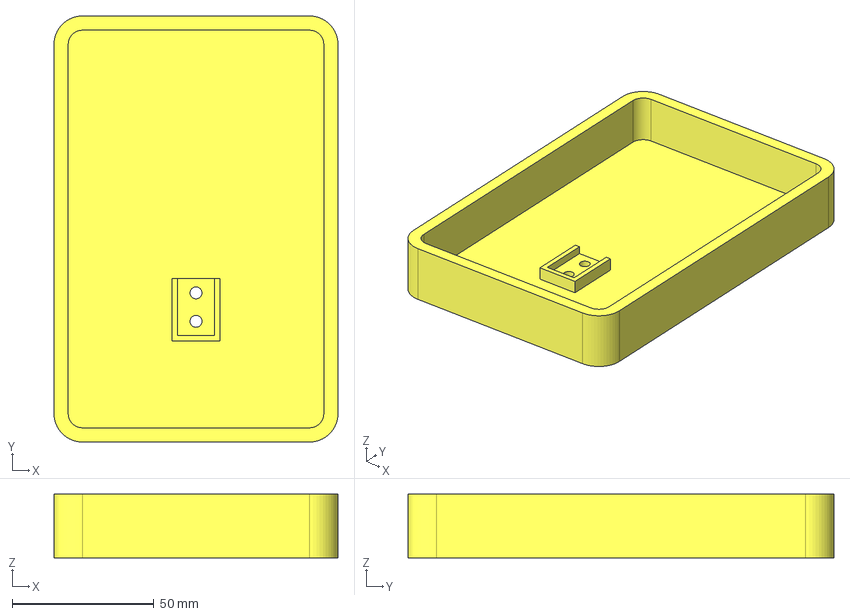
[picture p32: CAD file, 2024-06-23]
Hardware/Gehäuse/STEP/Scale_Top.step
100.0 x 150.0 x 22.4 mm

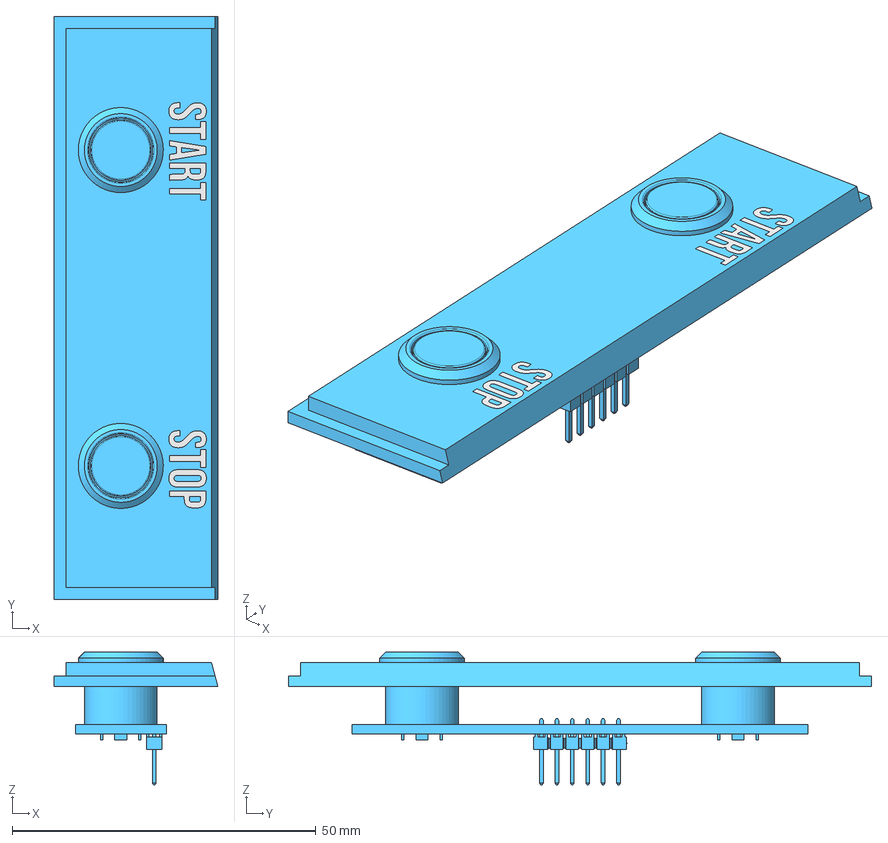
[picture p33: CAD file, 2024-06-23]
Hardware/Gehäuse/Ondsel(FreeCAD)/_Button.FCStd
27.0 x 96.0 x 21.9 mm
_STEP_PCB_Buttons_001
Buttons_001
Start_001
Stop_001

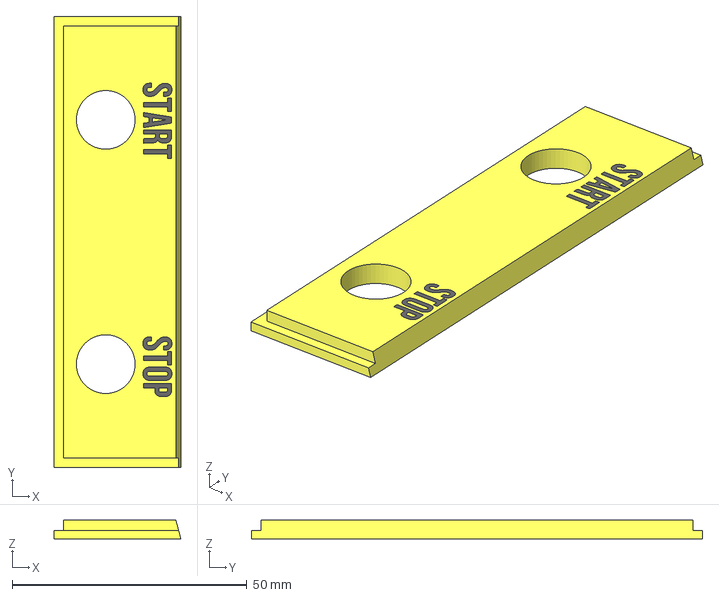
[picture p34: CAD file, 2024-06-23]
Hardware/Gehäuse/STEP/Button.step
27.0 x 96.0 x 4.00 mm

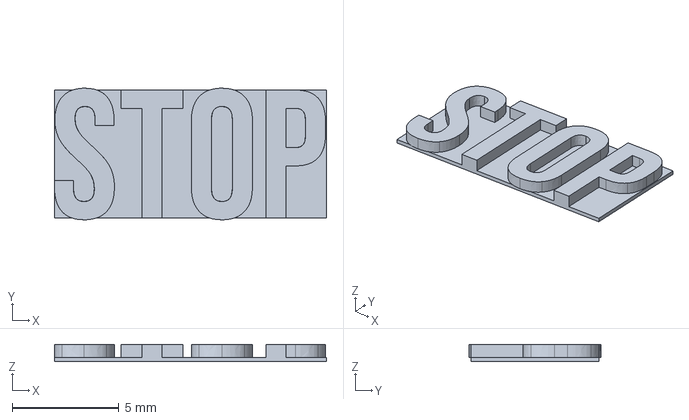
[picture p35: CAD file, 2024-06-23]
Hardware/Gehäuse/Ondsel(FreeCAD)/Stop.FCStd
12.8 x 6.17 x 0.8 mm

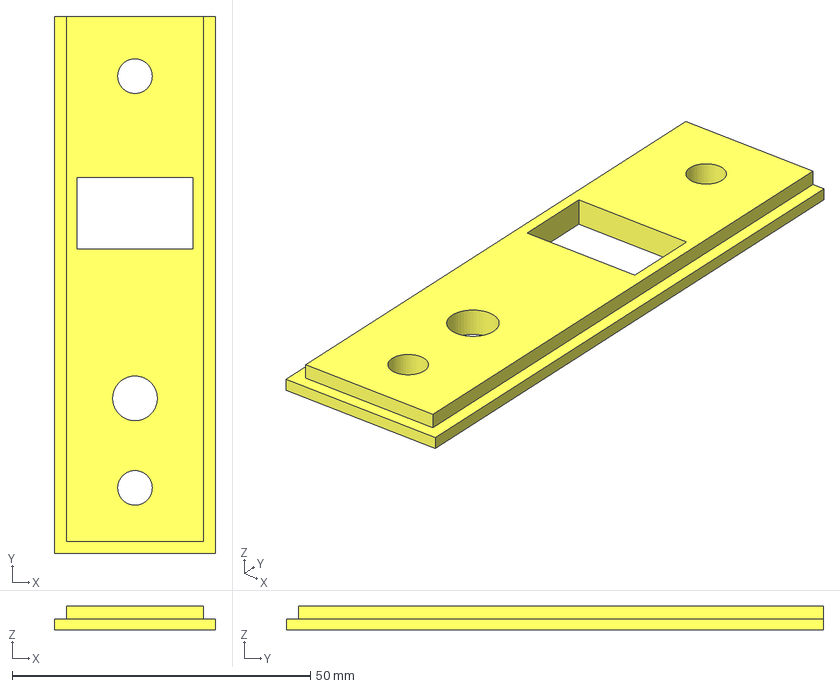
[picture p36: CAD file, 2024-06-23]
Hardware/Gehäuse/STEP/Rotary.step
27.0 x 90.0 x 4.00 mm

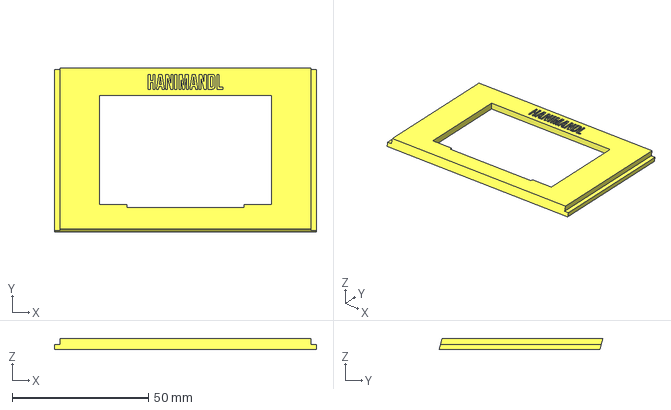
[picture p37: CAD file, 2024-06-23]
Hardware/Gehäuse/Ondsel(FreeCAD)/Display_OLED.FCStd
96.0 x 60.0 x 4.00 mm

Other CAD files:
Hardware/Gehäuse/STEP/Back_Small.step
Hardware/Gehäuse/STEP/Back_Big_1_USB.step
Hardware/Gehäuse/Ondsel(FreeCAD)/_STEP_PCB_Power.FCStd
Hardware/Gehäuse/STEP/Top.step
Hardware/Gehäuse/Ondsel(FreeCAD)/Back_Big_1.FCStd
Hardware/Gehäuse/Ondsel(FreeCAD)/Back_Big_2.FCStd
Hardware/Gehäuse/Ondsel(FreeCAD)/Bottom.FCStd
Hardware/Gehäuse/Ondsel(FreeCAD)/Buttons.FCStd
Hardware/Gehäuse/Ondsel(FreeCAD)/Display_TFT.FCStd
Hardware/Gehäuse/Ondsel(FreeCAD)/Rotary.FCStd
Hardware/Gehäuse/Ondsel(FreeCAD)/Scale_Top.FCStd
Hardware/Gehäuse/Ondsel(FreeCAD)/Start.FCStd
Hardware/Gehäuse/Ondsel(FreeCAD)/Top.FCStd
Hardware/Gehäuse/Ondsel(FreeCAD)/_Back_Big_1_USB.FCStd
Hardware/Gehäuse/Ondsel(FreeCAD)/_Display_OLED.FCStd
Hardware/Gehäuse/Ondsel(FreeCAD)/_Display_TFT.FCStd
Hardware/Gehäuse/Ondsel(FreeCAD)/_Rotary.FCStd
Hardware/Gehäuse/Ondsel(FreeCAD)/_STEP_PCB_Buttons.FCStd
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

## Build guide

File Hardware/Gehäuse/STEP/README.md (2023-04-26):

# HaniMandlWroom/Hardware/Gehäuse/STEP
HaniMandel für das Node MCU ESP32 38Pin Evaluation Board
## Was findet man in diesem Ordner
In diesem Ordner findet man alle STEP Files von dem HaniMandel Gehäuse und der Waage für den 3D-Druck

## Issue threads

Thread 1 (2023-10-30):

ROTARY_SCALE 2 small problem

Frank-Bemelman, 2023-10-30:
Hi there!

Tried your software. My rotary encoder gives 2 steps per click.
So I adjusted #define ROTARY_SCALE 2

When set to 1, it is difficult to navigate the setup menu, as it makes two steps per click of the rotary knob.
When set to 2, the navigation makes nice steps, but only the 4 first items are reachable.

So, around line #2970, I changed as shown below. Now, the full menu is accesible.

BTW, I also changed the direction of the knob, it seems to me that -1 for the step value gives an unnatural behaviour,
but I guess this might be personal. For me, a clockwise rotation should select in downwards fashion.

initRotaries(SW_MENU, lastpos, -1, MenuepunkteAnzahl, 1);
  while (modus == MODE_SETUP and (digitalRead(switch_setup_pin)) == HIGH) {
    if (rotaries[SW_MENU].Value < 0) {
      rotaries[SW_MENU].Value = (MenuepunkteAnzahl * ROTARY_SCALE) - 1;
    }
    else if (rotaries[SW_MENU].Value > ((MenuepunkteAnzahl * ROTARY_SCALE) - 1)) {
      rotaries[SW_MENU].Value = 0;
    }

Keep up the good work,
Cheers.
Frank

RolandRust, 2023-11-16:
Hello,
thx for the Input.
I tested the Rotary only with the KY-040. Maybe I should also order a HW-040 RSW.
I'll implement your changes and will test the Program.  You are right. The HW-040 makes 2 Input Signals per one step, so You will never reach the end of the Menu.
BR
Roli

RolandRust, 2024-02-04:
Should be now fixed in the Developer Branch. But not tested.

RolandRust, 2024-06-23:
Should be solved with the new release

RolandRust, 2024-06-23:
Should be solved with the new release

Closed 2024-06-23.

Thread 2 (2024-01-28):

HaniMandl upstream maintenance

amotl, 2024-01-28:
Dear Roland,

thank you for your excellent work over here, and a belated happy new year (it is still January, right?). ;]

We are finally and gradually getting back to maintaining the original code and project [^1], and would like to get in touch with you about it.

- https://github.com/hiveeyes/hani-mandl/issues/40

Coming from [^2], where you are also receiving praise from the community, would you be up to upstreaming your changes to the canonical spot, or do we have the permission to cherry-pick corresponding improvements?

We would love to build up some development nucleus together, but of course it is totally up to you. In any case, we appreciate any kind of help and support. Let us also know if you need any mutual support, and keep up the good work.

With kind regards,
Andreas.

[^1]: https://github.com/hiveeyes/hani-mandl
[^2]: https://community.hiveeyes.org/t/getting-hanimandl-out-into-the-world-hanimandl-raus-in-die-grosse-welt-werfen/5193

RolandRust, 2024-02-04:
Sent a eMail to amotl.

RolandRust, 2024-02-04:
Hi Andreas, yes, that is a good Idea, I love the open source development. And also I wish to Understand what should be the differents from the Comercial Version and the Open source version. till know I realiced what was in my "Brian" based on your Hanimandel Code.

amotl, 2024-02-04:
>> Join the crew at [community.hiveeyes.org](https://community.hiveeyes.org/)?
>
> That is a good Idea, I love the open source development.

Excellent. Feel free to join any time.

> Also I wish to understand about the differences between the commercial version and the open source version.

The commercial variant by @andreash-esp, demonstrated at https://hanimandl.de/, is another fork of the original version by Marc Vasterling. It is probably much more mature than the upstream FOSS variant, so the one maintained by Clemens|Hiveeyes is a bit left behind. Because Andreas' variant is closed source, we can't tell much about what's exactly inside, but we believe up until now it has been totally rewritten compared to the original.

amotl, 2024-02-04:
Thank you for joining, Roland.

At [Getting HaniMandl out into the world / Hanimandl raus in die grosse Welt werfen](https://community.hiveeyes.org/t/getting-hanimandl-out-into-the-world-hanimandl-raus-in-die-grosse-welt-werfen/5193), you already earned much praise, so feel free to share your email to me with the community right away, either on this discussion thread, or on behalf of a separate thread/topic within the [HaniMandl category](https://community.hiveeyes.org/c/hanimandl/78).

I think [@roidesreines](https://community.hiveeyes.org/u/roidesreines/summary) will be happy to see you around, and I also wish you a pleasant stay. Have fun!

Thanks again, closing this.

Closed 2024-02-04.

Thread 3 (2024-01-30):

Schematic pin numbers

salmancina, 2024-01-30:
Hi Roland,
Thank you very much for your excellent project.
I think there are some minor labelling issues on the schematic diagrams. The pin numbering on the esp32 from pins 20 to 38 are running from top to bottom rather than bottom to top.
Also the +3 and GND are transposed on the HX711 on some of the sheets.
Regards, Sal Mancina

RolandRust, 2024-02-08:
Hi Sal Mancina,
jepp, the ESP32 isn't nice nummered. I can change them if I change the schematic, but this symbol is not drawed nice. It was created for hand soldering. For the PCB version i would the pins group by function :-).
The pins for the HX711 can be confused.  As I started with the wired version i did not look to the pin number of the connector. The folder PCB  is an sepparat project.

salmancina, 2024-02-12:
Hi Roland,

Good to hear from you. I used your original project as the basis of my
build. Thank you very much for making it available. I am following your
development branch on GitHub and will try it when you think it is mature.

If it helps in any way I have attached a copy of my ino file. All the
onscreen displays are now in English. Perhaps you can try it as I have
changed some of the onscreen items to (I hope) make things clearer.

I haven't implemented the INA219, counters or multiple users so those parts
are not translated. Also the error messages are not translated yet, perhaps
that will come next.

Regards, Sal

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

Closed 2024-02-08.

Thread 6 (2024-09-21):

Automatic fill mode

Pukkahq, 2024-09-21:
If you have a jar fill weight of 500g. in automatic mode if it fills to 498g you remove the jar and put it down again it will automatically open the honey gate again. if the jar fill is 501g it does nothing.

RolandRust, 2024-09-23:
which version do you use? With version W.0.2 I have never seen that the servo opens again if you place a glass on it without pressing the start button.

Pukkahq, 2024-09-26:
W.0.2

We are in automatic mode.
Place a jar, press start.
If its under filled and you pick it up and put it back on the scales it will open the valve.

RolandRust, 2024-09-28:
I have now tested it with version W.0.2 and don't see the phenomenon. As you can see in the video, I have to press the start button so that the squeeze valve opens when a glass that has already been started is placed on the scale.
 https://youtu.be/VfxytLiSxO4

RolandRust, 2024-10-19:
I made now other experiments with exactly  498g, but I can not see the Issue that the honey gate open automatic after remove the Jar and put it again on the scale. Can you send my a Video in a case when this happens? when its a bug I have to know what you are doing. As long I can not reproduce this case it is not possible to solve this problem.

Pukkahq, 2024-10-20:
I will test again with the new DEV code and report back

Pukkahq, 2024-10-24:
I managed to get this to fail, but did not recored it.

The machine is in full automatic mode, press start, fill jar to 495g. lift jar and put back down slowly. start will appear on the display and the gate will open.

RolandRust, 2024-10-26:
I have now made several attempts to get the HM into this condition. Unfortunately I haven't been able to do it yet. I think you have to proceed a little systematically to find the error (there must be one)
In order for Start to appear on the display after picking up the glass and putting it back on, the following conditions must be met:
if (auto_aktiv == 1 && abs(gewicht) <= glastoleranz && servo_aktiv == 0 and turntable_ok == true and stop_wait_befor_fill == 0 and stop_button_close_dp == 0)
- auto_aktiv --> always 1 if in the full automatic mode
- abs(gewicht) --> Weight that is on the scale
- glastoleranz --> Your saved Value in the EEprom from the Setup - Automatic- Jar toleranze
- servo_aktiv --> will be set to 0 if you remove the jar from the scale
- turntable_ok --> always 1 if you do not use the turntable (new in W.0.03)
- stop_wait_befor_fill  --> always 0 if you do not use the turntable (new in W.0.03)
- stop_button_close_dp -->  always 0 if you do not use your recommend feature to fill something in the jar after the tare (new in W.0.03)
So we can ignore a lot of variables --> auto_aktiv, servo_aktiv, turntable_ok, stop_wait_befor_fill, stop_button_close_dp.
Now we have two left:  abs(gewicht) and glastoleranz
The Value glastoleranz is saved in the EEprom and has a Value between 0 and 99.
The Value abs(gewicht)  is the weight from the scale minus the saved value in the EEprom for the jar weight.
Even if you have 99g in the glass tolerance, we are still a long way away (ok 99 doesn't really make sense). There would be a maximum of 198g capacity at which the servo would be opened (a bit much but not the problem here, as we have well over 400g).
Fazit: Could be a SW Bug during using weak HW. Could try to evaluate the variable gewicht during a average value . makes the HM slower.

RolandRust, 2024-10-26:
there must be a value to get in the weight that's  wrong. can you send me a picture from your XH711 that you are using?

Closed 2024-11-16.

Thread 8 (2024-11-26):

scaletime not declared - when compiling with isDebug 5

KarlEffinger, 2024-11-26:
When compiling the source with
`#define isDebug 5`
there is a compilation error: `'scaletime' was not declared in this scope`
The error is caused by line 3588: `      Serial.print(" Dauer ");           Serial.print(millis() - scaletime);`
which belongs to procedure `void processAutomatik(void)`
"Scaletime" is defined once in line 2864 of procedure `void setupINA219(void)`, but not available outside.

RolandRust, 2024-11-26:
I will fix it. THX for the report

RolandRust, 2024-11-28:
Should be fixed

Closed 2024-11-28.

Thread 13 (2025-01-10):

ina219 setup screen issue

KarlEffinger, 2025-01-10:
Hi Roland,

when using the INA219 Setup I get the following screen mixmatch ("Winkel" in red letters on same location as "Strom" in white letters")
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
Additionally I need to use the "Abbrechen" option to end the calibration and return to main menu.

(In addition to this bug, I have a question: what's this calibration module doing? Is there any documentation to it (besides the source code), that I could read?

Thank you so much for this great adaption of the hani mandl! I finished my construction work for a printable housing and also made a (simple, one board only) pcb. Are you interested in any of these and maybe want to share it on your project page?

Regards Karl

RolandRust, 2025-01-12:
Hello Karl, I tested it at the weekend. It is actually the case that there is an error in the code. I'll correct it when I get the chance (but it might take a while since I'm currently in the process of dividing the code so that it's no longer all in one file.) The calibration doesn't actually do much. This only finds the minimum angle for closing the tap so that the servo does not press too hard on the screw. If you don't actually need it, you can also adjust it manually in the servo setting. Unfortunately I don't have any instructions. Because it's too much effort for me. Of course I'd be happy to take one if someone writes one. I'd rather invest my time in the code than in documentation :-) As far as the display output is concerned, there will be a major change anyway. I'm currently having massive problems with the TFT lib in conjunction with an ILI9488 display drive in combination with the ESP-S3 chip. (I still have something in mind with a 4 inch display with touch) If you have made a circuit board and a housing, you are welcome to send me the data (roland(at)greenmail.ch). I will then upload these to Git. Thank you very much for your report. It's always good when errors are found :-). Greetings Roli

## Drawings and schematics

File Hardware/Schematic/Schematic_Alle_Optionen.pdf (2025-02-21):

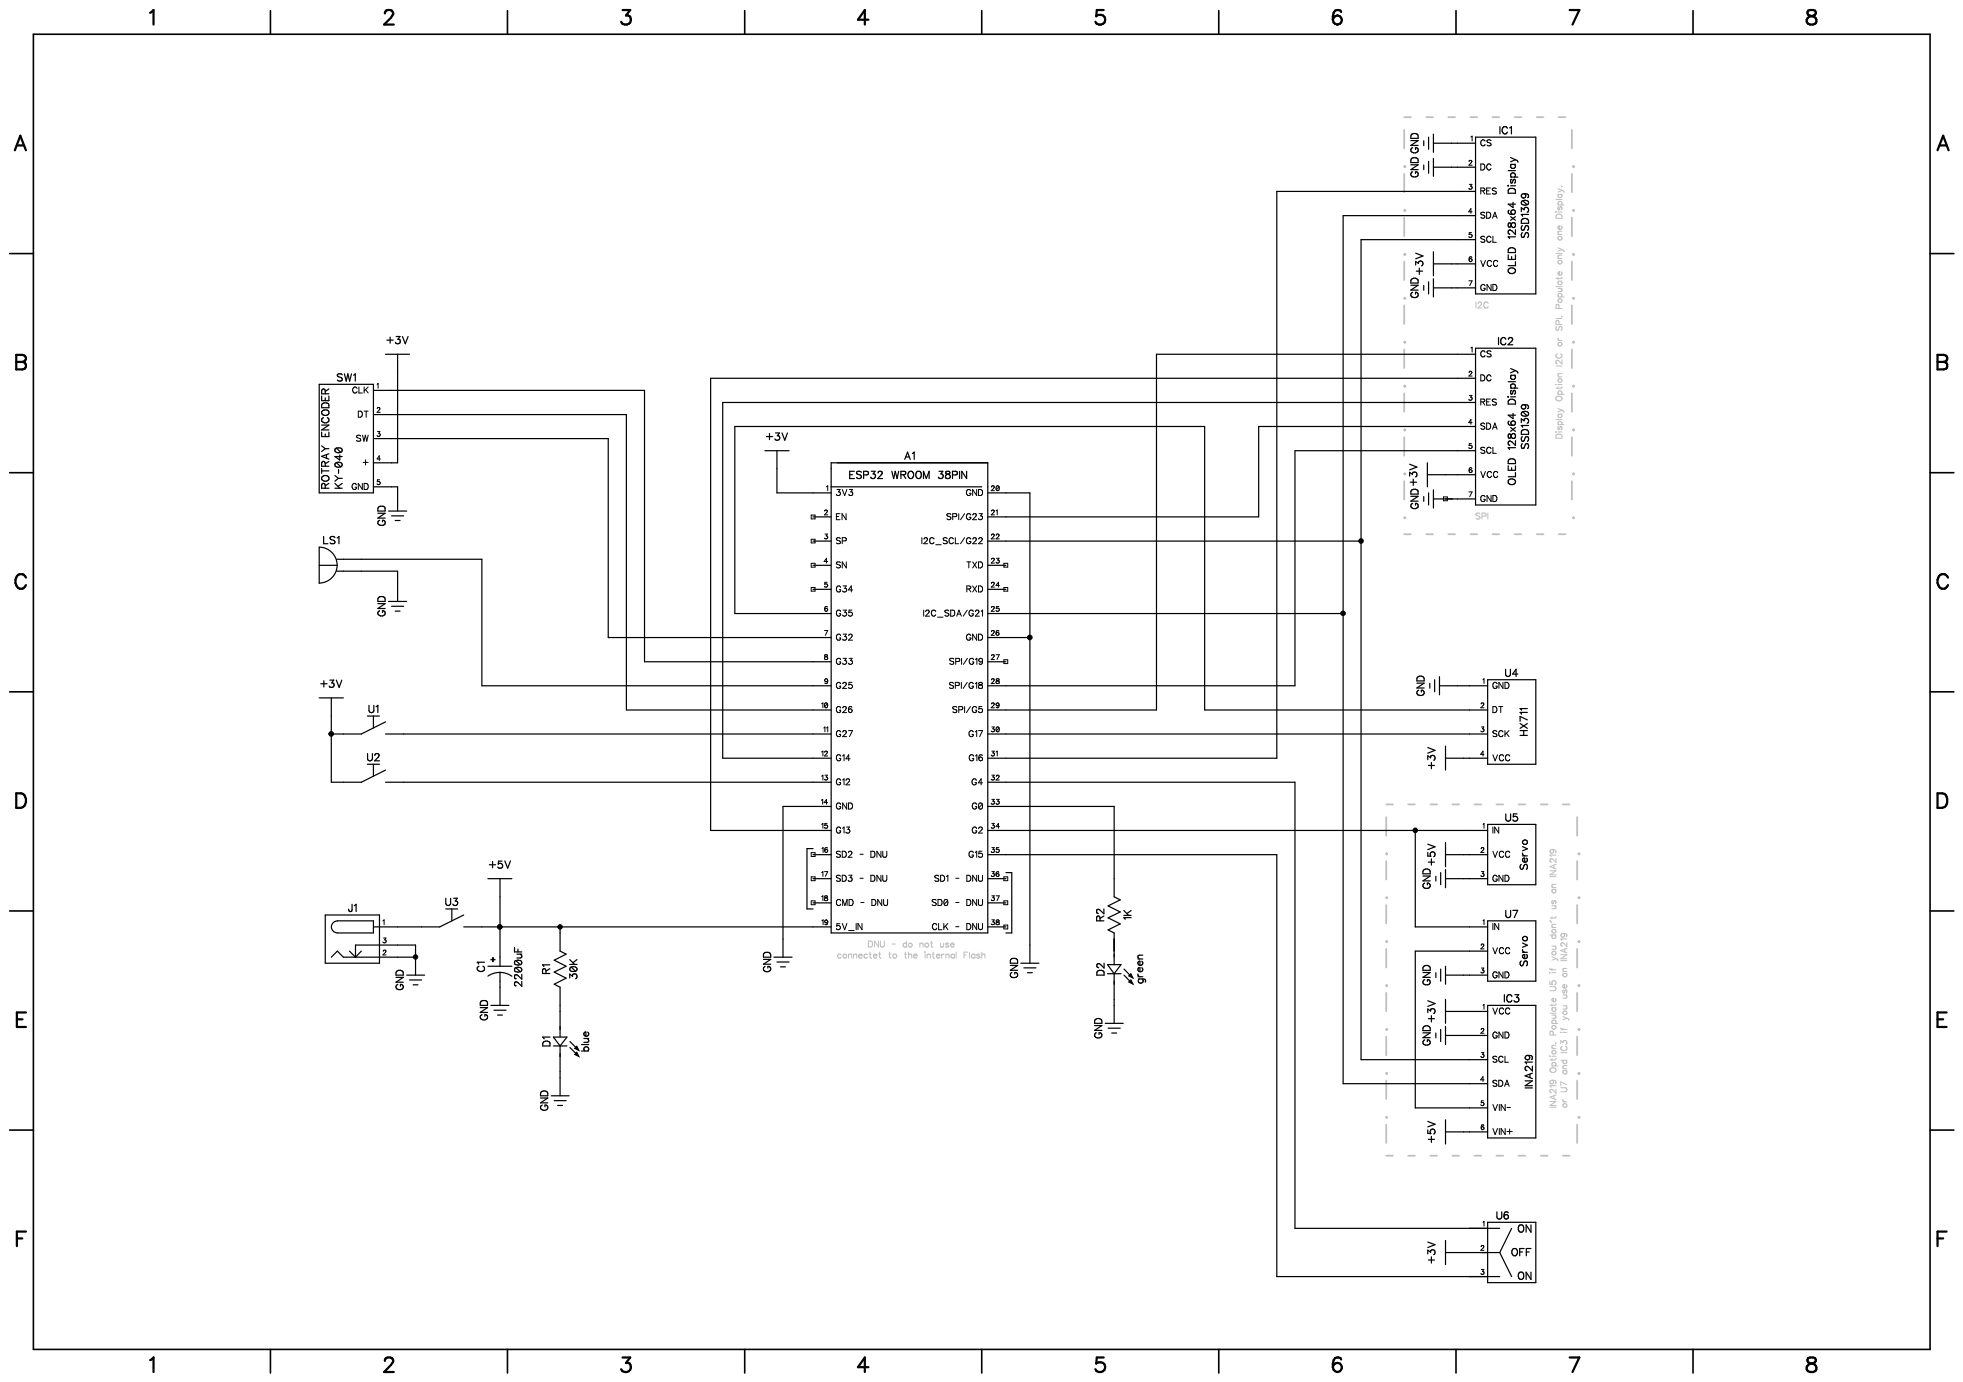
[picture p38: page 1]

- - - - - - - -Display Option I2C or SPI. Populate only one Display.

- - - - - - - - -INA219 Option. Populate U5 if you don't us an INA219 or U7 and IC3 if you use an INA219

DNU - do not use

connectet to the internal Flash

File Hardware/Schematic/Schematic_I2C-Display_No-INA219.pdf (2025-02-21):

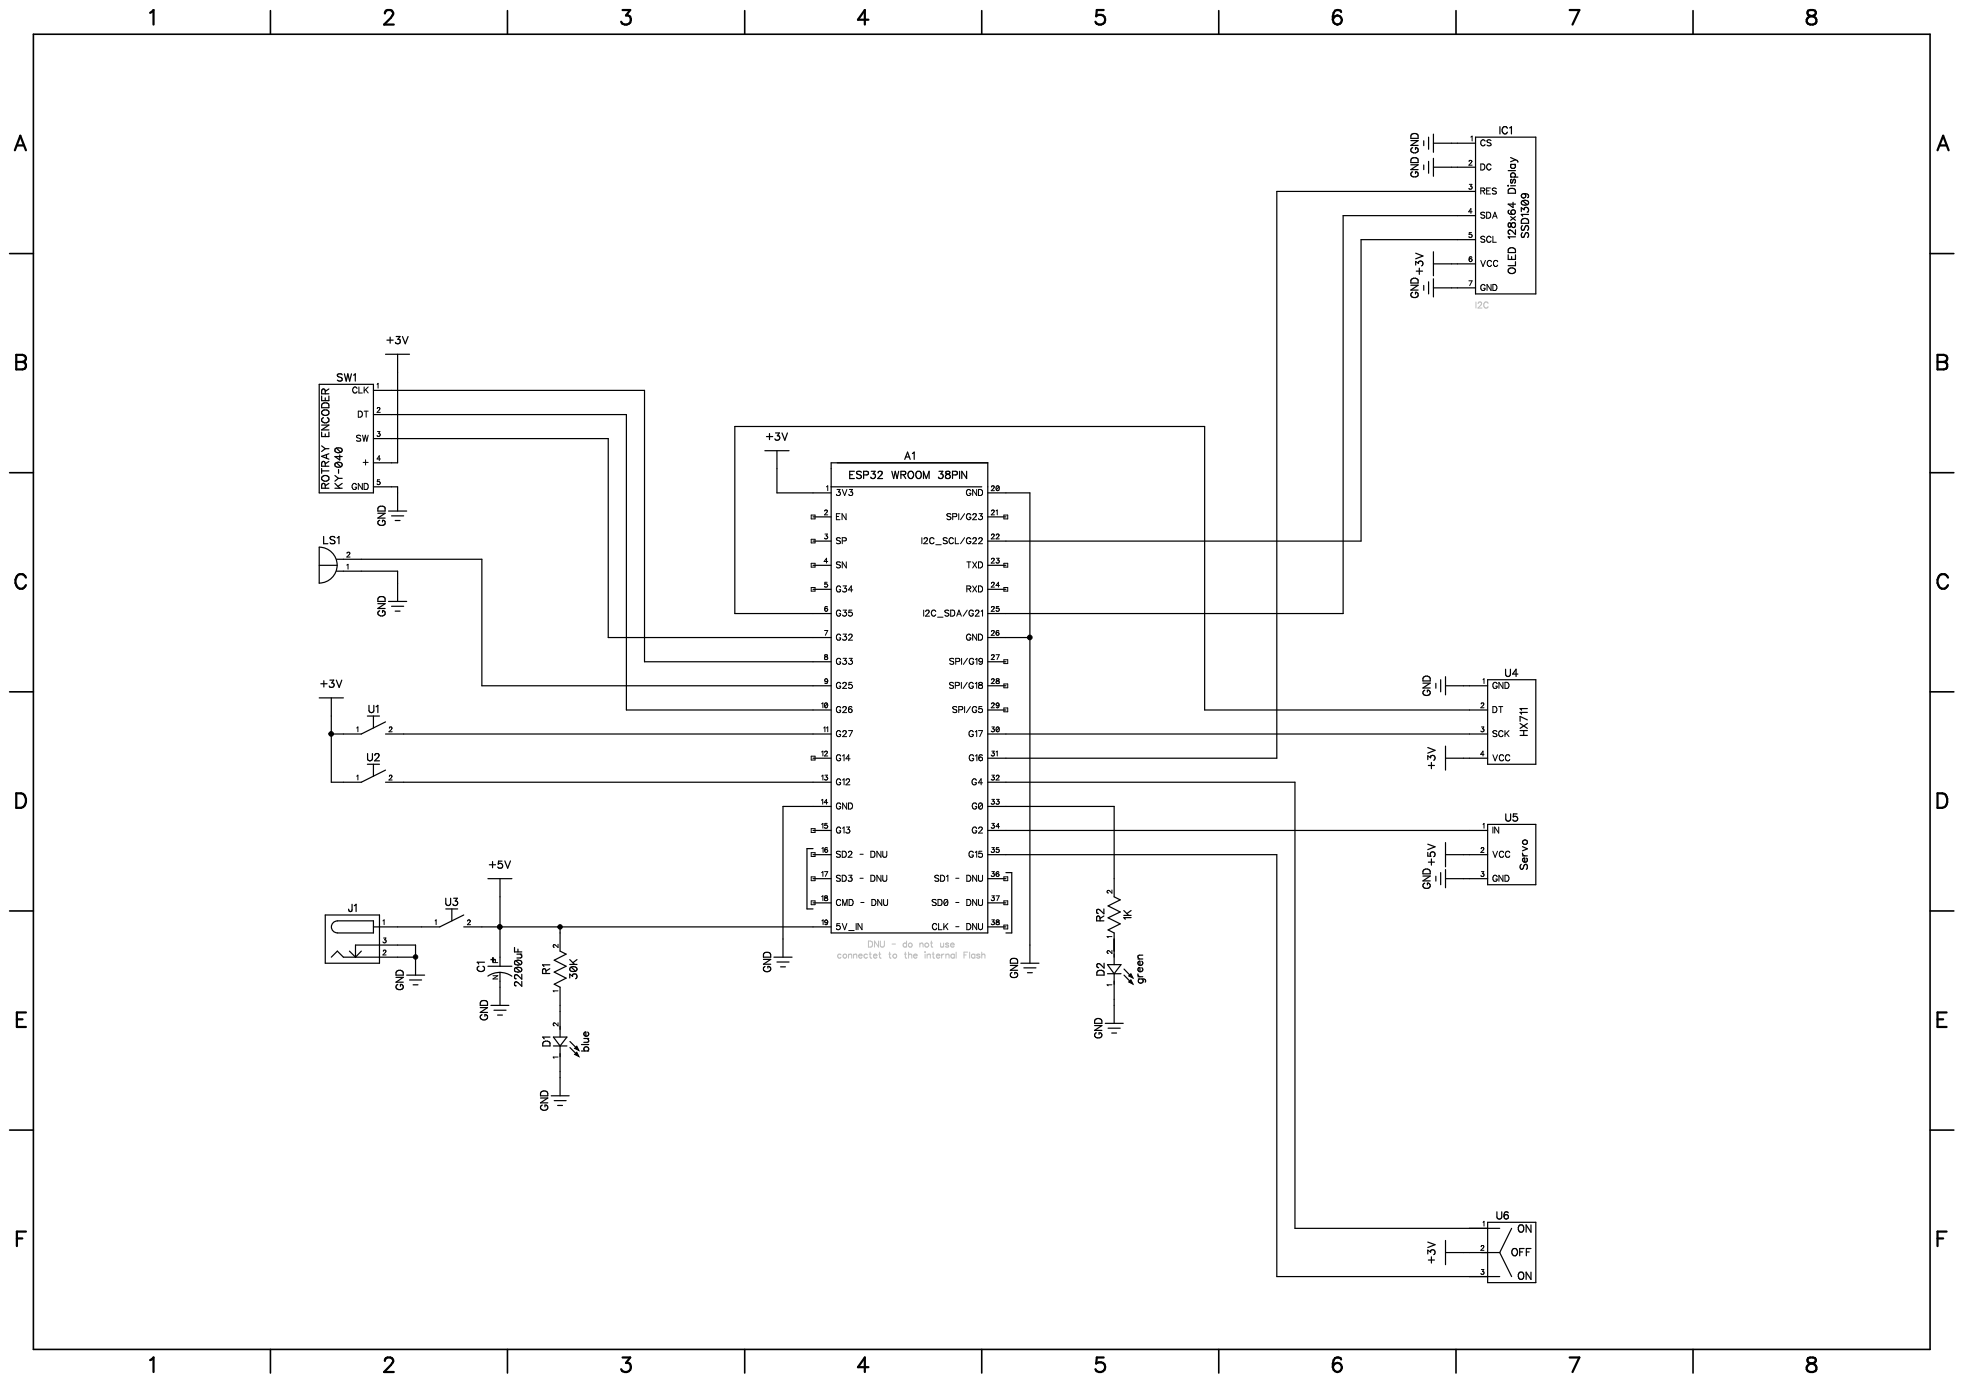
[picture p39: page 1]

DNU - do not use

connectet to the internal Flash

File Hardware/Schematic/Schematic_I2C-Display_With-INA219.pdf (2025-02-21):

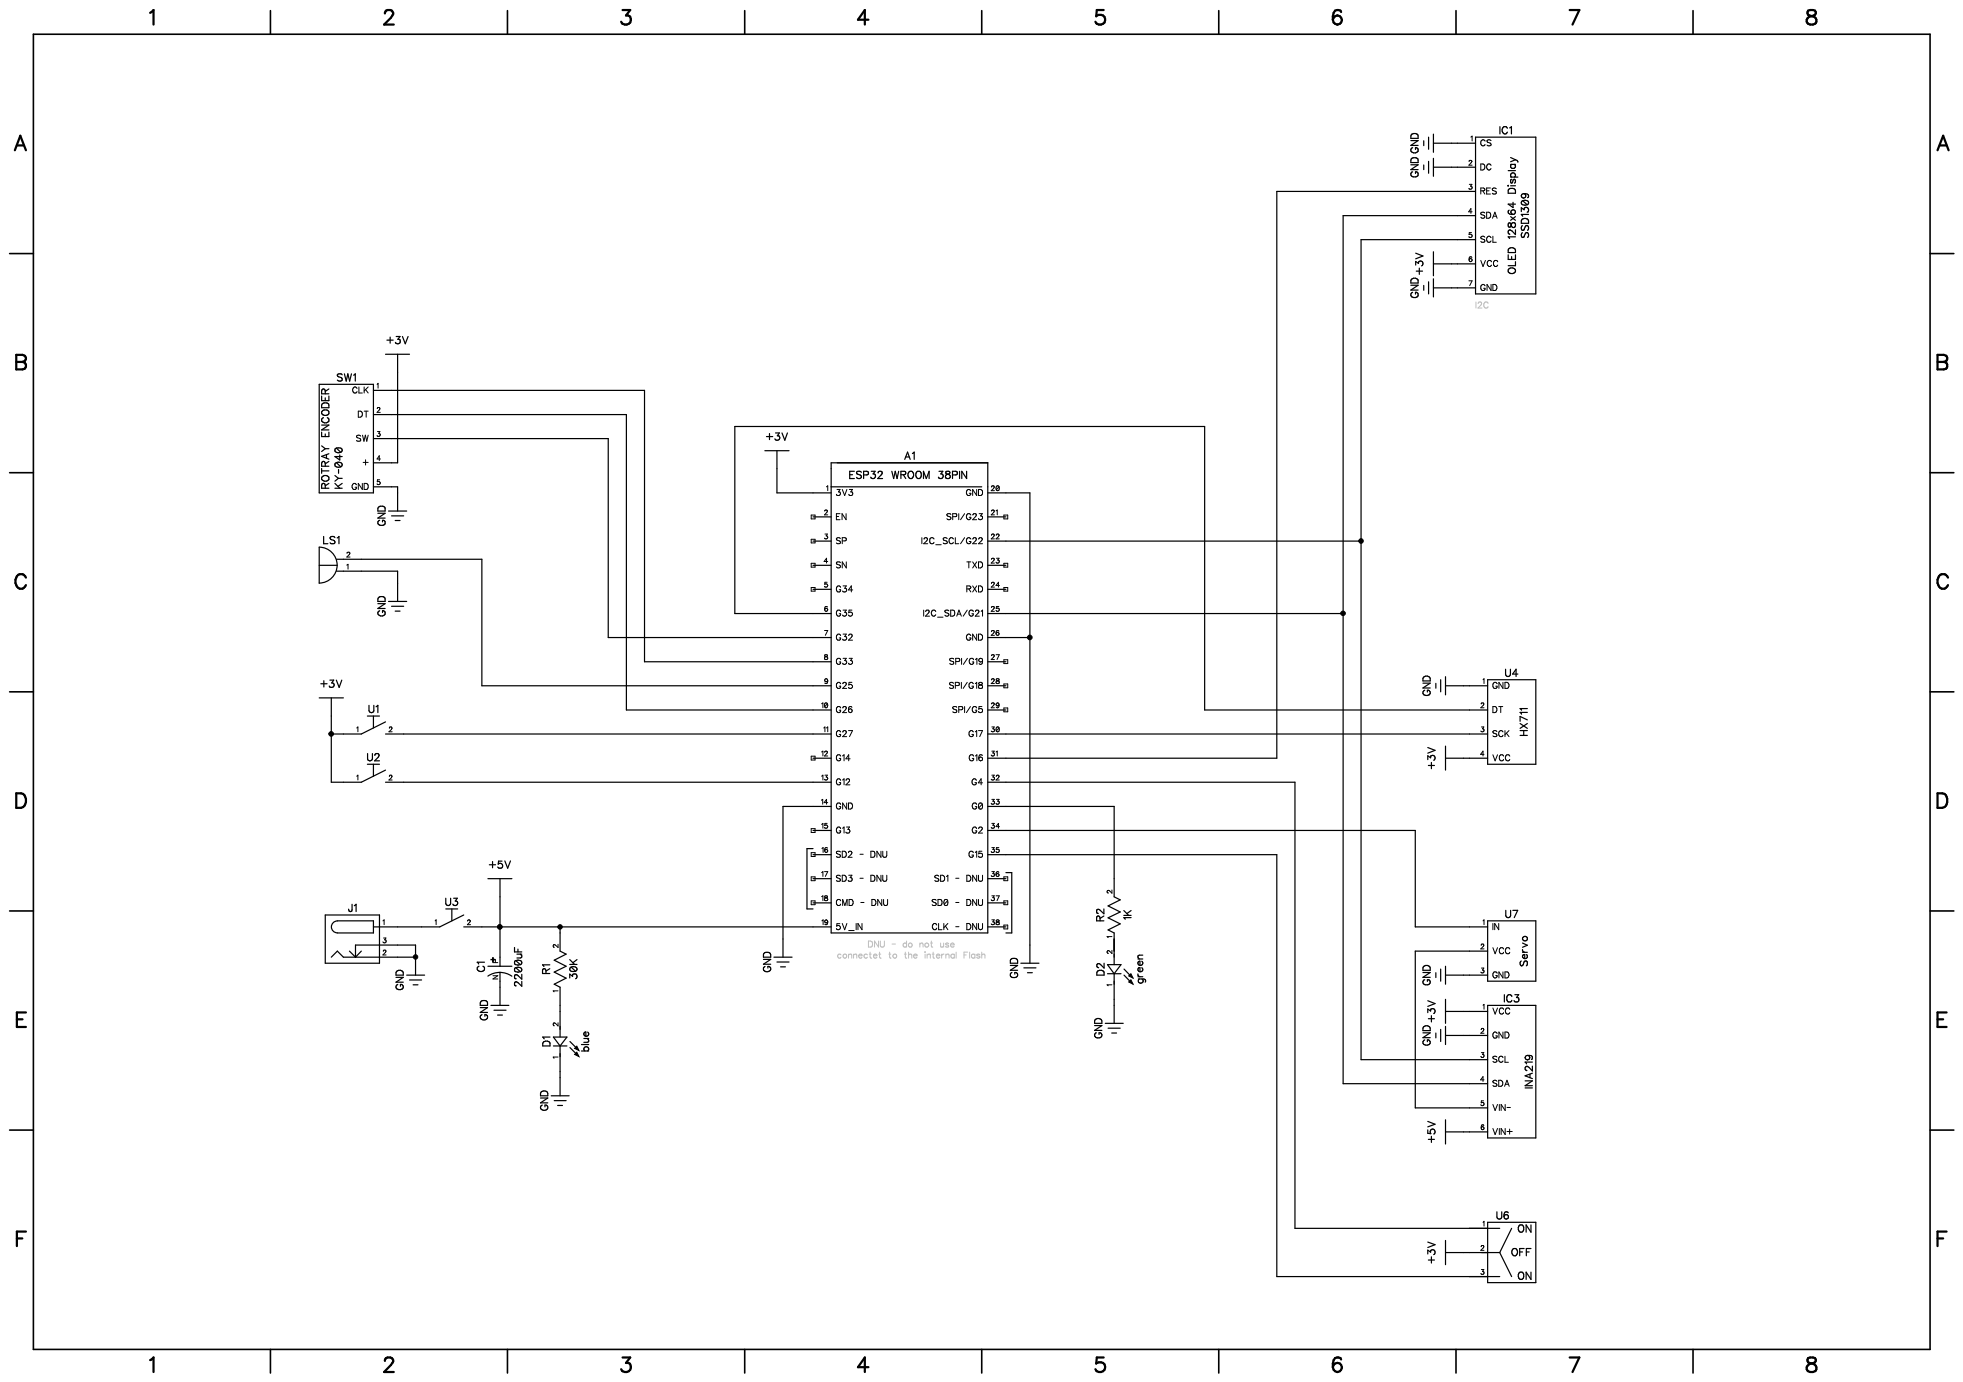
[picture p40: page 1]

DNU - do not use

connectet to the internal Flash

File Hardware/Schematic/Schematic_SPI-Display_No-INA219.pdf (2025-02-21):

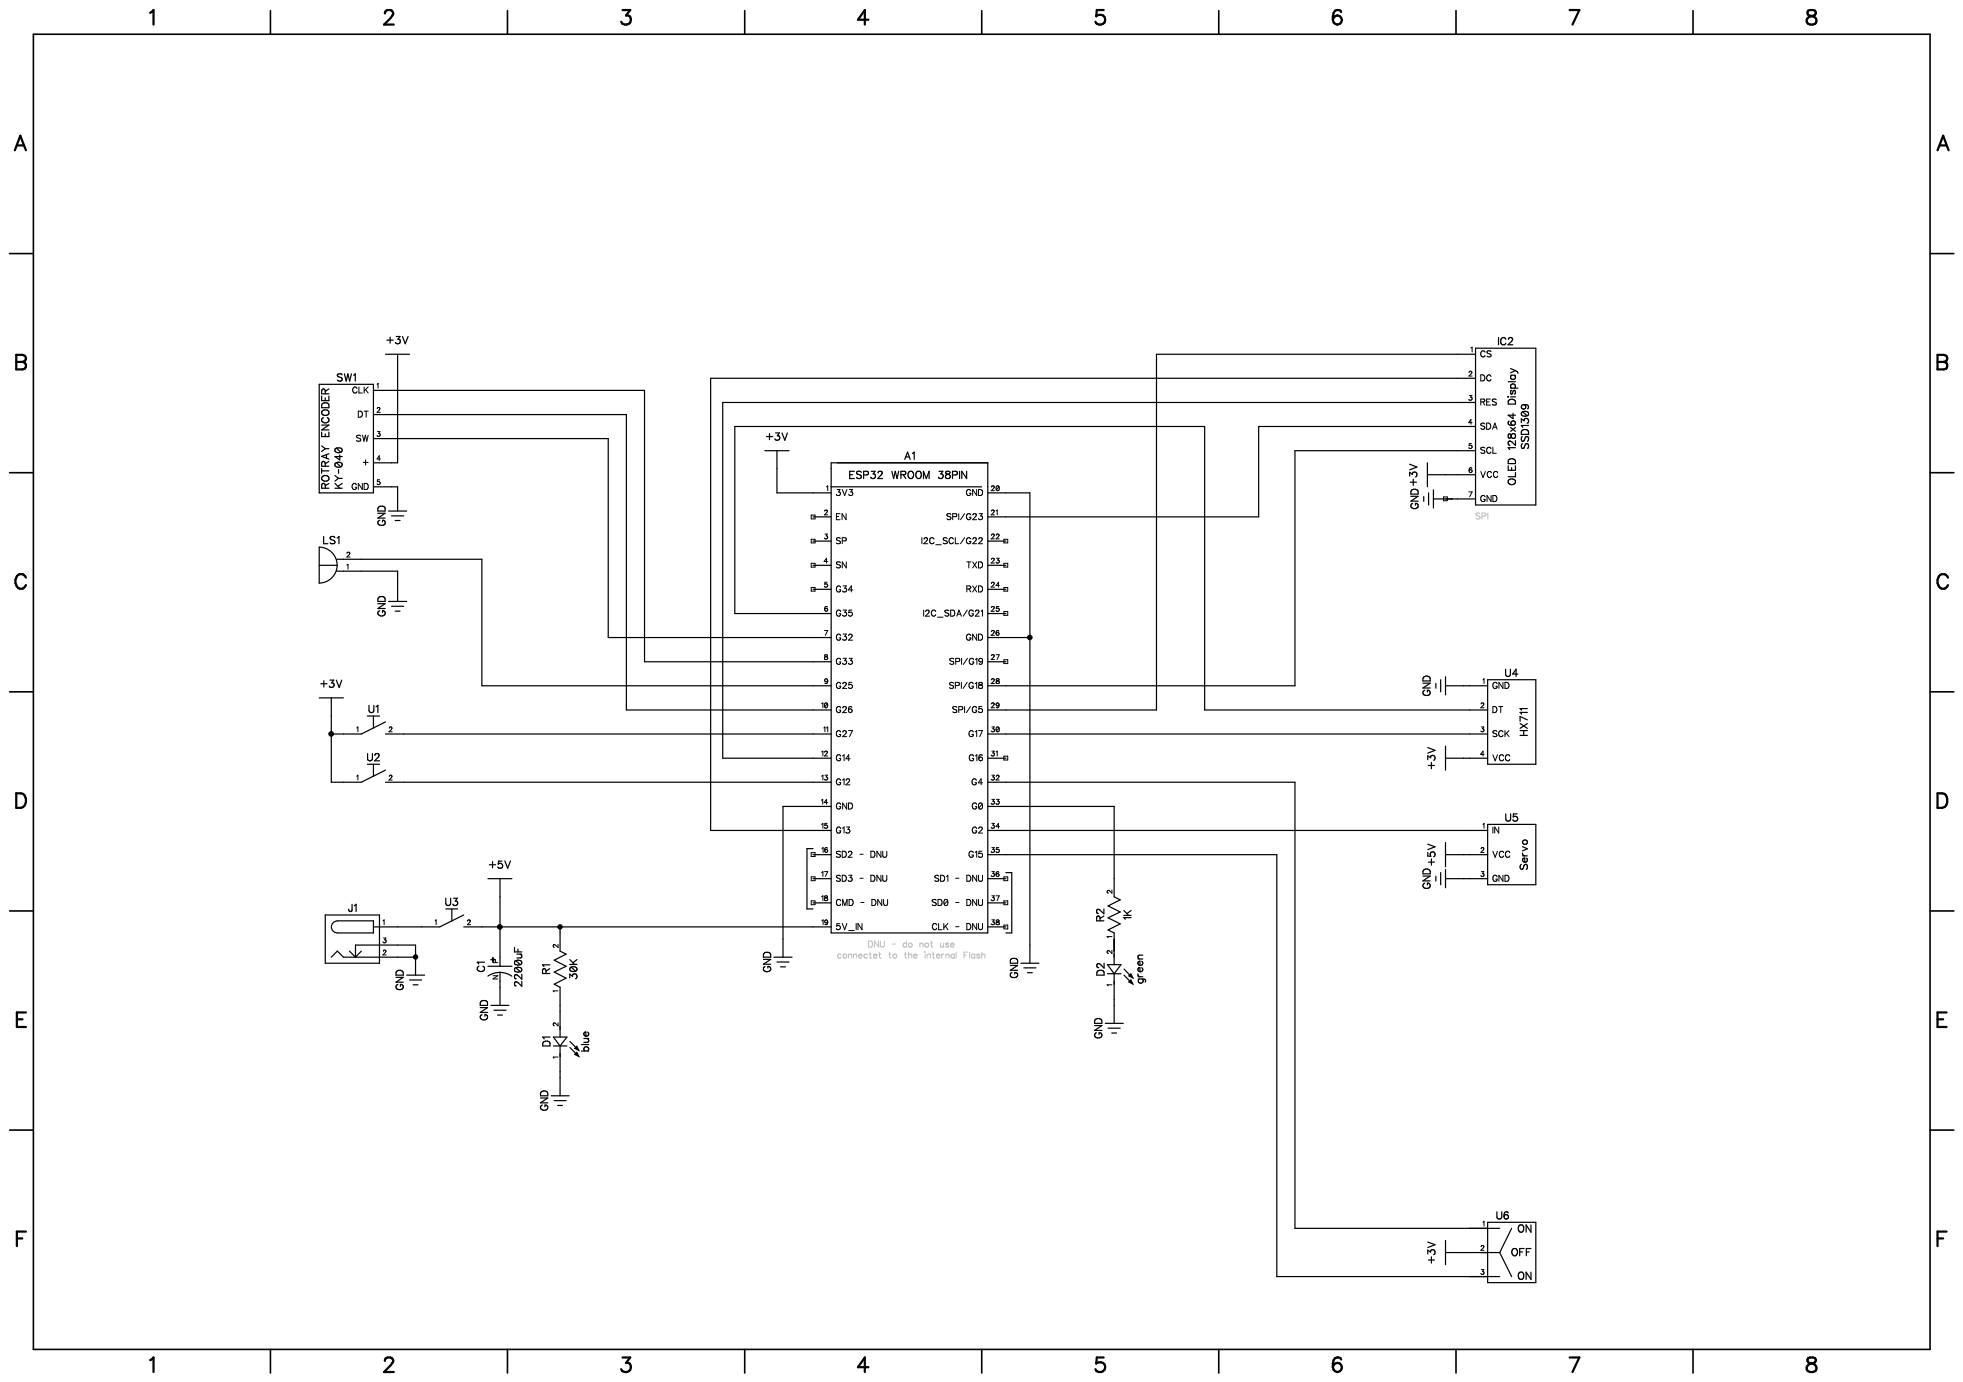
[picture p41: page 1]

DNU - do not use

connectet to the internal Flash

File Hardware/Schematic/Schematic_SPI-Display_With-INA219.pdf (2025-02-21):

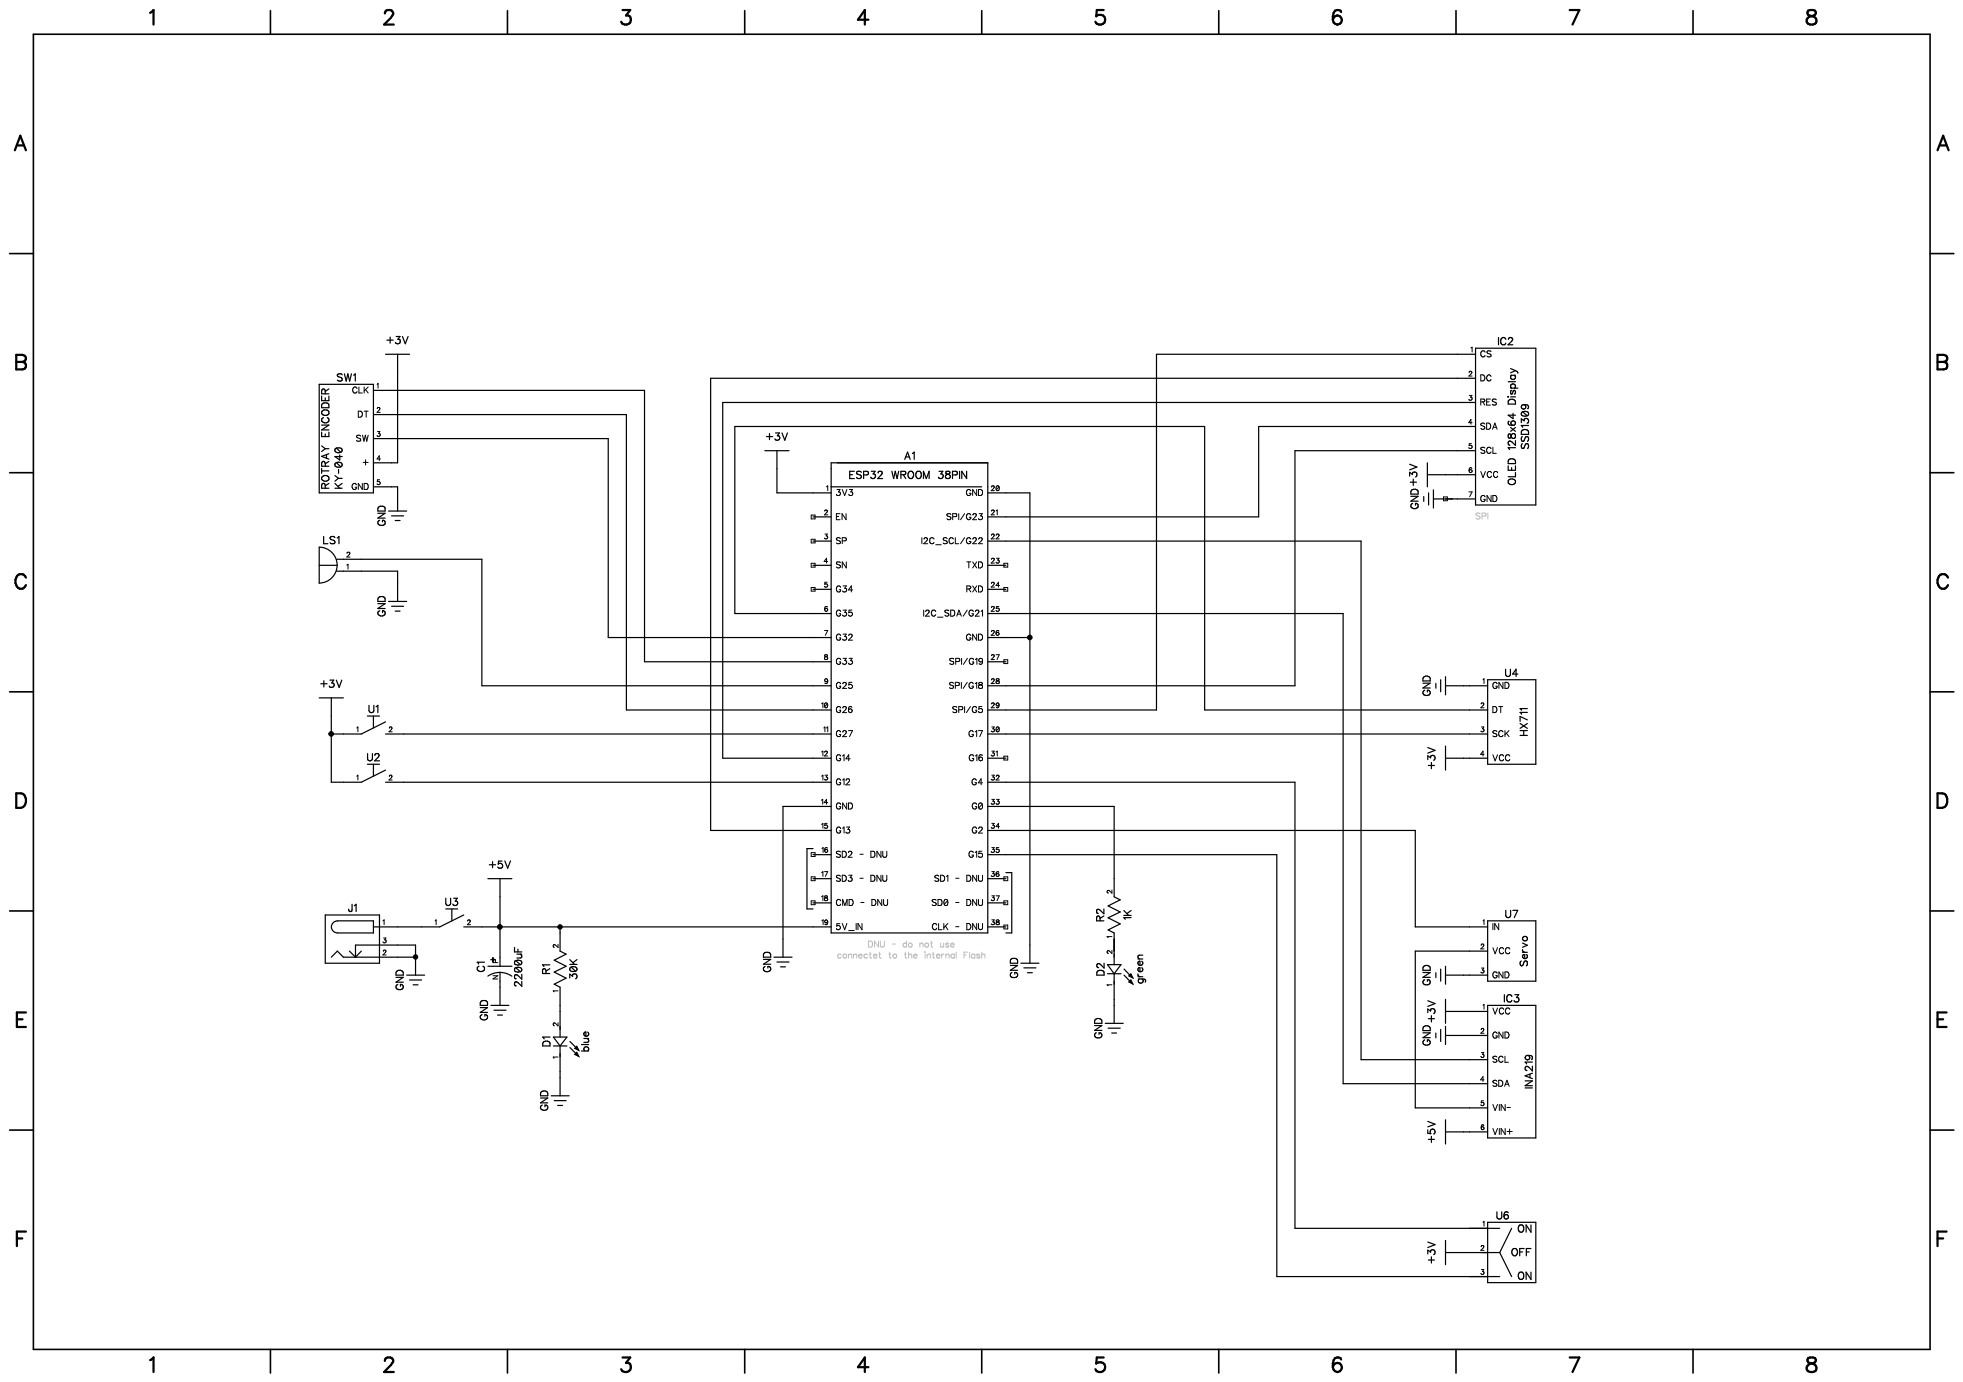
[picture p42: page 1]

DNU - do not use

connectet to the internal Flash

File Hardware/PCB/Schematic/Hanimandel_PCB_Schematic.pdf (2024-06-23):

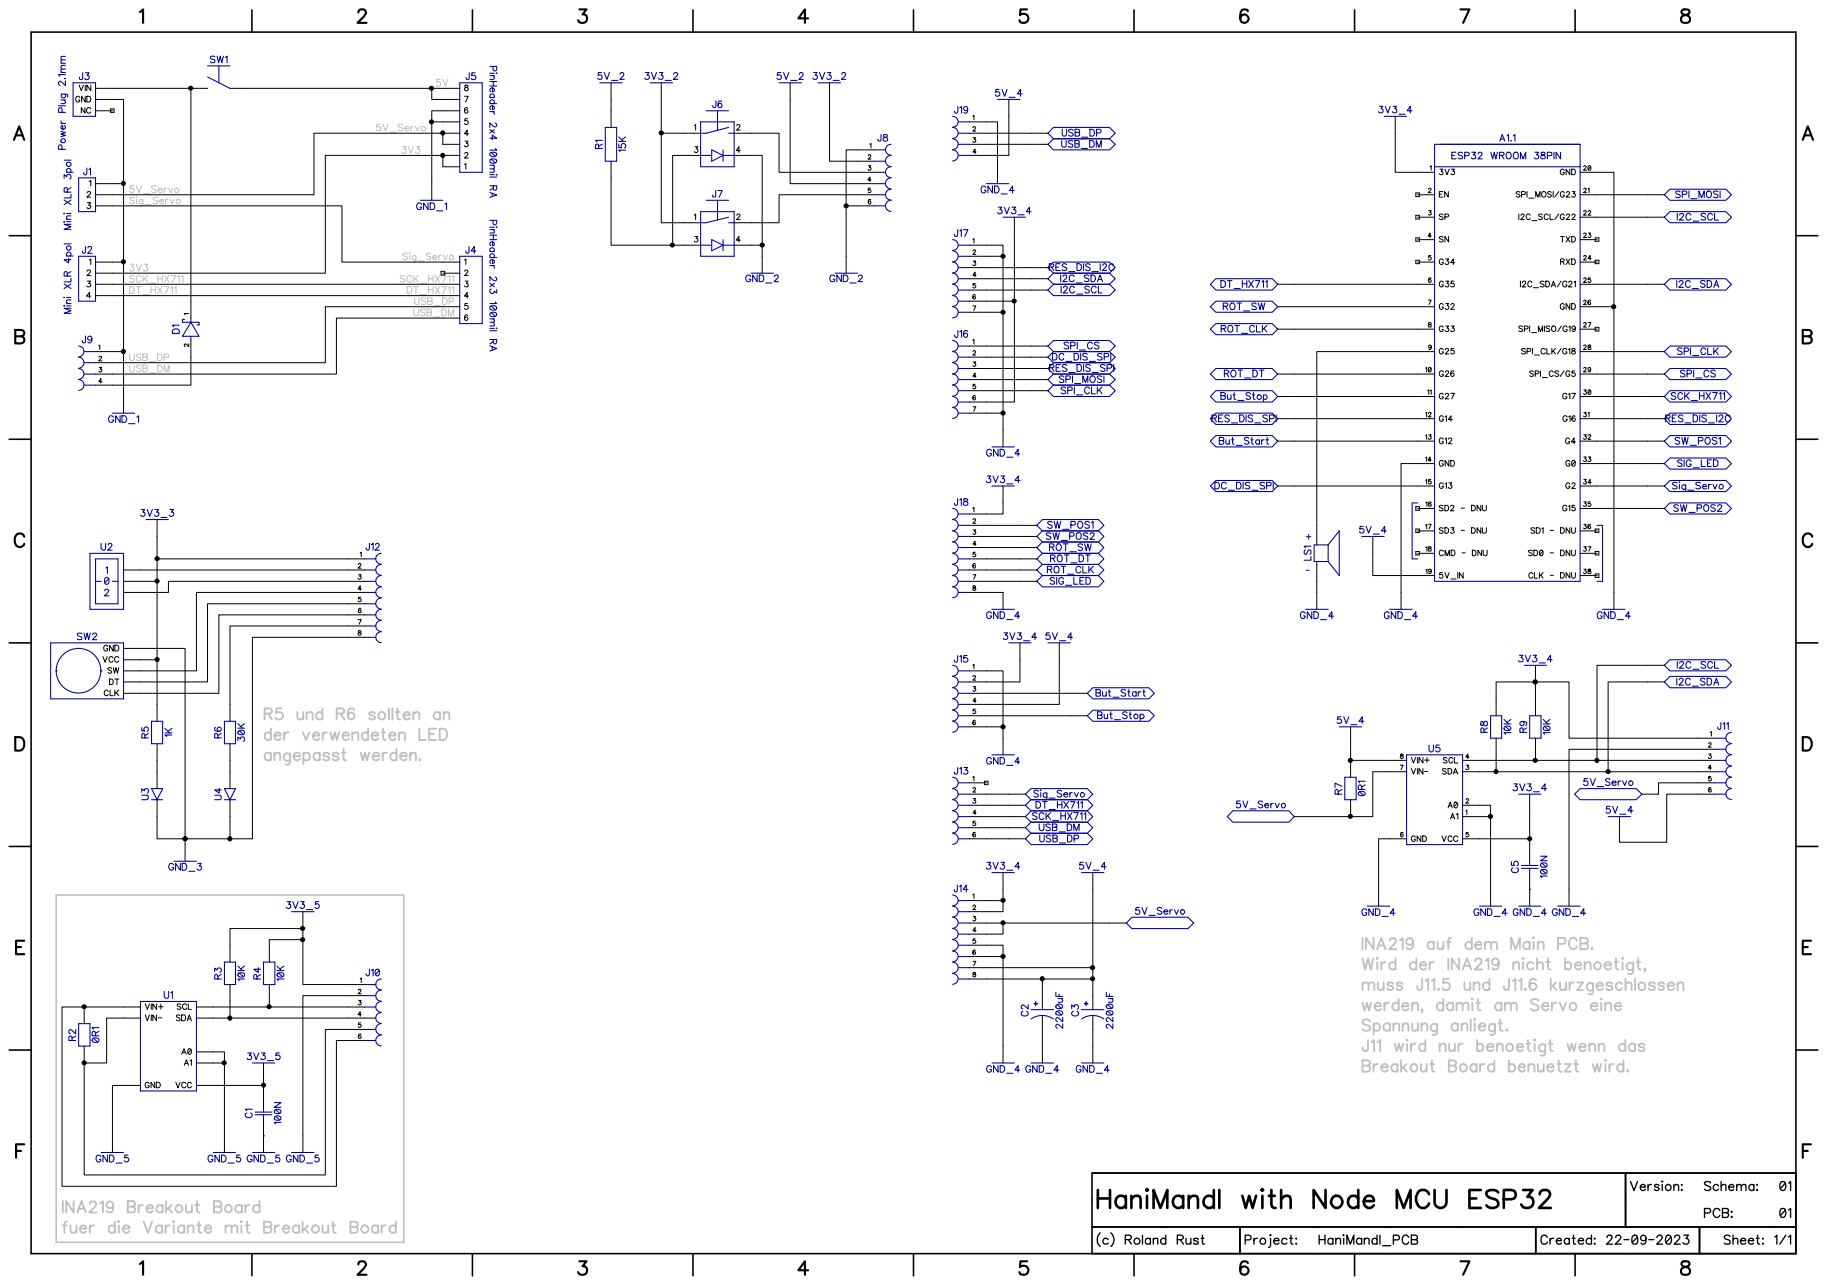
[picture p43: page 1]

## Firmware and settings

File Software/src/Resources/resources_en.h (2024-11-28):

char LANGUAGE1[]            = "Language";
char LANGUAGE2[]            = "English";

//Process Setup
char TAREVALUES[]			= "Tarevalues";
char CALIBRATION[]			= "Calibration";
char FILL_QUANTITY[]		= "Fill quantity";
char AUTOMATIC[]			= "Automatic";
char SERVOSETTINGS[]		= "Servosettings";
char PARAMETER[]			= "Parameter";
char COUNTER[]				= "Counter";
char COUNTER_TRIP[]			= "CounterTrip";
char CLEAR_PREFS[]			= "Clear Prefs";				//Clear Preferences
char INA219_SETUP[]			= "INA219 Setup";

//Setup Tarevalues
char TAREVALUES_JAR[]		= "Tarevalues jars";			//DISPLAY:	Tarevalues jars
char MISSING[]				= "missing";				    //		    missing

//Setup Calibration
//Please empty the scale and confirm with OK
char PLEASE_EMPTY_THE[]		= "Please empty the";			//DISPLAY:	Please empty the
char SCALE_AND_CONFIRM[]	= "scale and confirm";			//		    scale and confirm
char WITH_OK_1[]			= "with OK";				    //		    with OK
//Please set up {value} and confirm with OK
char PLEASE_SET_UP[]		= "Please set up";			    //DISPLAY:	Please set up
char AND_CONFIRM[]			= "and confirm";			    //		    {500g} and confirm
char WITH_OK_2[]			= "with ok";				    //		    with ok

//Setup quantity jars
char FILL_QUANTITY_JARS[]	= "Fill quantity jars";

//Setup Automatik
char AUTOSTART[]			= "Autostart";
char JAR_TOLERANCE[]		= "Jar tolerance";
char CORRECTION[]			= "Correction";
char AUTOCORRECTION[]		= "Autocorrection";
char KINDNESS[]				= "-> Kindness";
char FLOW_G_OVER_TIME[]		= "Flow g/time";
char WAIT_BEFOR_FILL[]		= "Wait befor fill";

//Setup Servo
char LIVESETUP[]			= "Livesetup";
char MINIMUM[]				= "Minimum";
char FINEDOSAGE[]			= "Finedosage";
char MAXIMUM[]				= "Maximum";

//Setup Parameter
char BUZZER[]				= "Buzzer";
char LED_1[]				= "LED";                            //Variable LED is used in the Library from the Heltec Module :-(
char SHOW_LOGO[]			= "Show logo";
char SHOW_CREDITS[]			= "Show credits";
char COLORSCHEME[]			= "Colorscheme";
char MARKER_COLOR[]			= "Marker color";

//Setup INA219
char SERVO_CURRENT[]	    = "Servo current";
char CAL_HONEY_GATE[]		= "Cal. honey gate";				//Calibrate honey gate
char SHOW_CURRENT[]			= "Show current";
char MAX_CURRENT[]			= "max. current";
char MIN_ANGLE[]			= "min. angle";
char CALIBRATION_RUNNING[]	= "Calibration running";
char CURRENT[]				= "Current";
char ANGLE[]				= "Angle";
char HONEY_GATE[]			= "Honey gate";
char CALIBRATION_DONE[]		= "Calibration done";

//Setup Clear Preferenzes
char CLEAR_PREFERENCES[]	= "Clear Preferences";
char CLEAR_NVS_MEMORY[]		= "Clear NVS memory";
char RESET_TURNTABLE[]	    = "Reset turntable";

//Setup Turntable
char TURNTABLE[]            = "Turntable";
char INIT_TURNTABLE[]       = "Init Turntable";
char SETUP_TURNTABLE[]      = "Setup Turntable";
char SETUP_DRIPPRODECTION[] = "Setup Dripprodection";
//char ADJUST_JAR_POS[]       = "Adjust jar  pos.";			//Adjust jar  position
//char STEPS[]                = "Steps";
//char POSITION[]             = "Position";
char MOVE_JAR[]             = "Move jar";
char SPEED_INIT[]           = "Speed init";
char SPEED_RUN[]            = "Speed run";
char MOVE_POS[]             = "Move Position";
char SETUP_STEPPER[]        = "Setup stepper";
char SETUP_SERVO[]          = "Setup servo";
char OKKAY[]                = "ok";                         //ok [max 3 letters]
char NOKAY[]                = "nok";                        //not ok [max 3 letters]
char CENTER_JAR[]           = "Center jar";
char OPEN_DRIPPROTECTION[]  = "Open Dripprod.";             //open Dripprodection
char CLOSE_DRIPPROTECTION[] = "Close Dripprodection";       //close Dripprodection
char SPEED_DRIPPROTECTION[] = "Speed Dripprodection";       //speed Dripprodection
char WAIT_TO_CLOSE_DP[]     = "Wait to close DP";           //wait to open Dripprodection
char DP_MIN_ANGLE[]         = "DP min angle";               //Dripprodection min angle
char DP_MAX_ANGLE[]         = "DP max angle";               //Dripprodection max angle
//Connection failed
char CONNECTION[]           = "Connection";                 //Display: Connection
char FAILED[]               = "failed";                     //         failed
//Close drip protection wait time reading failed
char CLOSE_DRIP_DP[]        = "Close drip";                 //Diaplay: Close drip
char PROTECTION_WAIT_DP[]   = "protection wait";            //         protection wait
char TIME_READING_DP[]      = "time reading";               //         time reading
char FAILED_DP[]            = "failed";                     //         failed
char ENABLE_OTA_UPDATE[]    = "Enable OTA Update";

//Setup About
char ABOUT[]                = "About";
char VERSION[]              = "Version";
char MAC[]                  = "MAC";                        //MAC adress
char WLAN_CHANNEL[]         = "WLAN channel";
char USE_TURNTABLE[]        = "Use Turntable";
char OTA_UPDATE[]           = "OTA update";

//Warnings
//no scale!
char NO[] 				    = "no";							//DISPLAY:	no
char SCALE[]				= "scale!";						//		    scale!
//not calibrated
char NOT[]				    = "not";						//DISPLAY:	not
char CALIBRATED[]			= "calibrated";					//          calibrated
//empty the scale
char EMPTY[]				= "empty";						//DISPLAY:	empty
char THE_SCALE[]			= "the scale!";					//		    the scale!

//Manual Modus
char MANUAL[]				= "Manual";
char SERVO[]				= "Servo";
char TARE[]				    = "Tare";
char INA[]				    = "INA";                        //do not translate
char CURR[]				    = "Curr.";                      //Current
char MAX_1[]				= "max";
char ACTUAL[]				= "Actual";
char A_UPPER_CASE[]			= "A";							//[Angle - only OLED display]

//Automatic Modus
char INA219[]				= "INA219";                     //do not translate
char AUTOCORR[]				= "Autocorr.";					//[no space for Autocorrection]
char MIN[]				    = "Min";						//[max 3 letters]
char MAX_2[]				= "Max";						//[max 3 letters]
char ACT[]				    = "Act";						//[max 3 letters - no space for Actual]
//Please put up the jar
char PLEASE_PUT[]			= "Please put";					//DISPLAY:	Please put
char UP_THE_JAR[]			= "up the jar";					//	    	up the jar
char TARE_JAR[]				= "Tare jar";
//Continue with the start button
char CONTINUE_WITH[]        = "Continue with";              //DISPLAY:  Continue with
char THE_START_BUTTON[]     = "the start button";           //          the start button
char FLOW[]				    = "Flow:";
char AS[]				    = "AS";							//[Autostart - only OLED Display]
char A_LOWER_CASE[]			= "a";							//[angle or auto - only OLED Display]
char C_LOWER_CASE[]			= "c";							//[correction - only OLED Display]
char F_LOWER_CASE[]			= "f";							//[flow - only OLED Display]


char NO_TARE[]				= "no tare!";

char OFF[]				    = "off";
char ON[]				    = "on";
char DARK[]				    = "dark";
char LIGHT[]				= "light";
char TOTAL[]				= "Total";
char RESET[]				= "Reset";
char ABORT[]				= "Abort";
char START[]				= "Start";
char OPEN[]				    = "open";
char CLOSE[]				= "close";
char BACK[]				    = "Back";
char SAVE[]				    = "Save";

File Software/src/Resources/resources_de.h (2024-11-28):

char LANGUAGE1[]            = "Sprache";
char LANGUAGE2[]            = "Deutsch";

//Process Setup
char TAREVALUES[]           = "Tarawerte";
char CALIBRATION[]          = "Kalibrieren";
char FILL_QUANTITY[]        = "Füllmenge";
char AUTOMATIC[]            = "Automatik";
char SERVOSETTINGS[]        = "Servoeinst.";
char PARAMETER[]            = "Parameter";
char COUNTER[]              = "Zählwerk";
char COUNTER_TRIP[]         = "ZählwerkTrip";
char CLEAR_PREFS[]          = "Clear Prefs";
char INA219_SETUP[]         = "INA219 Setup";

//Setup Tarevalues
char TAREVALUES_JAR[]       = "Tarawerte Gläser";
char MISSING[]              = "fehlt";

//Setup Calibration
char PLEASE_EMPTY_THE[]     = "Bitte Waage leeren";
char SCALE_AND_CONFIRM[]    = "und mit OK";
char WITH_OK_1[]            = "bestätigen";
char PLEASE_SET_UP[]        = "Bitte";
char AND_CONFIRM[]          = "aufstellen und mit";
char WITH_OK_2[]            = "OK bestätigen";

//Setup quantity jars
char FILL_QUANTITY_JARS[]   = "Füllmenge Gläser";

//Setup Automatik
char AUTOSTART[]            = "Autostart";
char JAR_TOLERANCE[]        = "Glastoleranz";
char CORRECTION[]           = "Korrektur";
char AUTOCORRECTION[]       = "Autokorrektur";
char KINDNESS[]             = "-> Kulanz";
char FLOW_G_OVER_TIME[]     = "Fluss g/Zeit";
char WAIT_BEFOR_FILL[]		= "Warte vor füllen";

//Setup Servo
char LIVESETUP[]            = "Livesetup";
char MINIMUM[]              = "Minimum";
char FINEDOSAGE[]           = "Feindosierung";
char MAXIMUM[]              = "Maximum";

//Setup Parameter
char BUZZER[]               = "Summer";
char LED_1[]                = "LED";
char SHOW_LOGO[]            = "Zeige Logo";
char SHOW_CREDITS[]         = "Zeige Credits";
char COLORSCHEME[]          = "Farbschema";
char MARKER_COLOR[]         = "Zeiger Farbe";

//Setup INA219
char SERVO_CURRENT[]        = "Servo Strom";
char CAL_HONEY_GATE[]       = "Cal. Quetschhan";
char SHOW_CURRENT[]         = "Zeige Strom";
char MAX_CURRENT[]          = "max. Strom";
char MIN_ANGLE[]            = "min. Winkel";
char CALIBRATION_RUNNING[]  = "Kalibration läuft";
char CURRENT[]              = "Strom";
char ANGLE[]                = "Winkel";
char HONEY_GATE[]           = "Quetschhan";
char CALIBRATION_DONE[]     = "Kalibration beendet";

//Setup Clear Preferenzes
char CLEAR_PREFERENCES[]    = "Lösche Preferences";
char CLEAR_NVS_MEMORY[]     = "Lösche NVS Speicher";
char RESET_TURNTABLE[]	    = "Reset Drehteller";

//Setup Turntable
char TURNTABLE[]            = "Drehteller";
char INIT_TURNTABLE[]       = "Init Drehteller";
char SETUP_TURNTABLE[]      = "Setup Drehteller";
char SETUP_DRIPPRODECTION[] = "Setup Tropfschutz";
//char ADJUST_JAR_POS[]       = "Glas Pos. anpassen";
//char STEPS[]                = "Schritte";
//char POSITION[]             = "Position";
char MOVE_JAR[]             = "Verschiebe Glas";
char SPEED_INIT[]           = "Init Geschw.";
char SPEED_RUN[]            = "Run Geschw.";
char MOVE_POS[]             = "Verschiebe Pos.";
char SETUP_STEPPER[]        = "Setup Schrittmotor";
char SETUP_SERVO[]          = "Setup Servo";
char OKKAY[]                = "ok";
char NOKAY[]                = "nok";
char CENTER_JAR[]           = "Zentriere Glass";
char OPEN_DRIPPROTECTION[]  = "Öffne Tropfschutz";
char CLOSE_DRIPPROTECTION[] = "Schliesse Tropfschutz";
char SPEED_DRIPPROTECTION[] = "Geschwindigkeit";
char WAIT_TO_CLOSE_DP[]     = "Wartezeit schliessen";
char DP_MIN_ANGLE[]         = "TS min Winkel";
char DP_MAX_ANGLE[]         = "TS max Winkel";
char CONNECTION[]           = "Verbindung";
char FAILED[]               = "fehlgeschlagen";
char CLOSE_DRIP_DP[]        = "Lesen Wartezeit";  
char PROTECTION_WAIT_DP[]   = "zum Schliessen";
char TIME_READING_DP[]      = "des Tropfschutzes";
char FAILED_DP[]            = "fehlgeschlagen";
char ENABLE_OTA_UPDATE[]    = "OTA-Update aktivieren";

//Setup About
char ABOUT[]                = "Über";
char VERSION[]              = "Version";
char MAC[]                  = "MAC";
char WLAN_CHANNEL[]         = "WLAN Kanal";
char USE_TURNTABLE[]        = "Benütze Drehteller";
char OTA_UPDATE[]           = "OTA Update";

//Warnings
char NO[]                   = "Keine";
char SCALE[]                = "Waage!";
char NOT[]                  = "Nicht";
char CALIBRATED[]           = "kalibriert";
char EMPTY[]                = "Waage";
char THE_SCALE[]            = "leeren!";

//Manual Modus
char MANUAL[]               = "Manuell";
char SERVO[]                = "Servo";
char TARE[]                 = "Tara";
char INA[]                  = "INA";
char CURR[]                 = "Strom";
char MAX_1[]                = "max";
char ACTUAL[]               = "Istwert";
char A_UPPER_CASE[]         = "W";

//Automatic Modus
char INA219[]               = "INA219";
char AUTOCORR[]             = "Autokorr.";
char MIN[]                  = "Min";
char MAX_2[]                = "Max";
char ACT[]                  = "Ist";
char PLEASE_PUT[]           = "Bitte Glas";
char UP_THE_JAR[]           = "aufstellen";
char TARE_JAR[]             = "Tara Glas";
char CONTINUE_WITH[]        = "Weiter mit";
char THE_START_BUTTON[]     = "der Start Taste";
char FLOW[]                 = "Fluss";
char AS[]                   = "AS";
char A_LOWER_CASE[]         = "a";
char C_LOWER_CASE[]         = "k";
char F_LOWER_CASE[]         = "f";

char NO_TARE[]              = "kein Tara!";

char OFF[]                  = "aus";
char ON[]                   = "ein";
char DARK[]                 = "dunkel";
char LIGHT[]                = "hell";
char TOTAL[]                = "Summe";
char RESET[]                = "Rücksetzen";
char ABORT[]                = "Abbrechen";
char START[]                = "Start";
char OPEN[]                 = "offen";
char CLOSE[]                = "zu";
char BACK[]                 = "Zurück";
char SAVE[]					= "Speichern";

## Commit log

2023-06-14 Add files via upload
    changed TFT display size
    [BoM.xlsx]
2023-07-27 Bottom Part für die PCB Variante vorbereitet
    [Bottom.step]
2023-09-19 Delete Hardware/PCB/BoM/Hanimandl_PCB_BoM.csv
    falsche Bestellnummer beim JST Stecker
    [Hanimandl_PCB_BoM.csv]
2024-08-04 Add files via upload
    Drehteller funktioniert, hat aber noch einige kleinere Bugs. z.B. Der Tropschutz geht nicht zu wenn die Stopp Taste gedrückt wird. Der Automatik Betrieb ist aber getestet und scheind zu funktionieren. Habe aber im Moment keinen Bock weiterzumachen für die öffentlichkeit. Für mich funktioniert es. Aber solange es im Imterei und Technik FB Forum so einen Kritiker gibt welcher immer alles besser weiss und der noch gelikt wird vin dem HM entwikler, da sage ich nur soll er es doch besser machen :-). mache das ja für mich :-)
2025-08-27 R2 und R7 korrigiert
    [Hanimandl_PCB_BoM.csv]
